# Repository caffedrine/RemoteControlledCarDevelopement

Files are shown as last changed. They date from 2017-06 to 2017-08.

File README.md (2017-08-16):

## RC Car Developement

Designing and implementing a remote controlled rover from zero to hero!

## Summary:
  1. Project information: [RC_Car_WordDoc.odt](docs/RC_Car_Developement.odt)
  2. Required list of components: [here](Components.md)
  3. How to build: [here](How-to-build.md)
  4. Firmware upload and debugging: [here](Firmware-upload.md)
  
*Costs:* ~60EUR

## Results

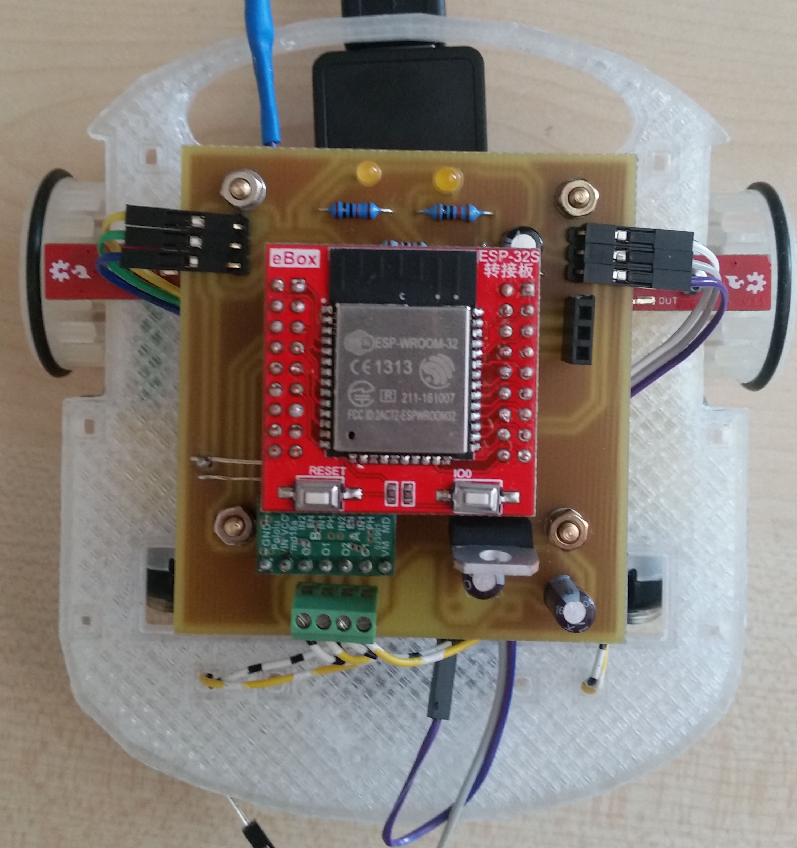
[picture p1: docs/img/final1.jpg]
final1

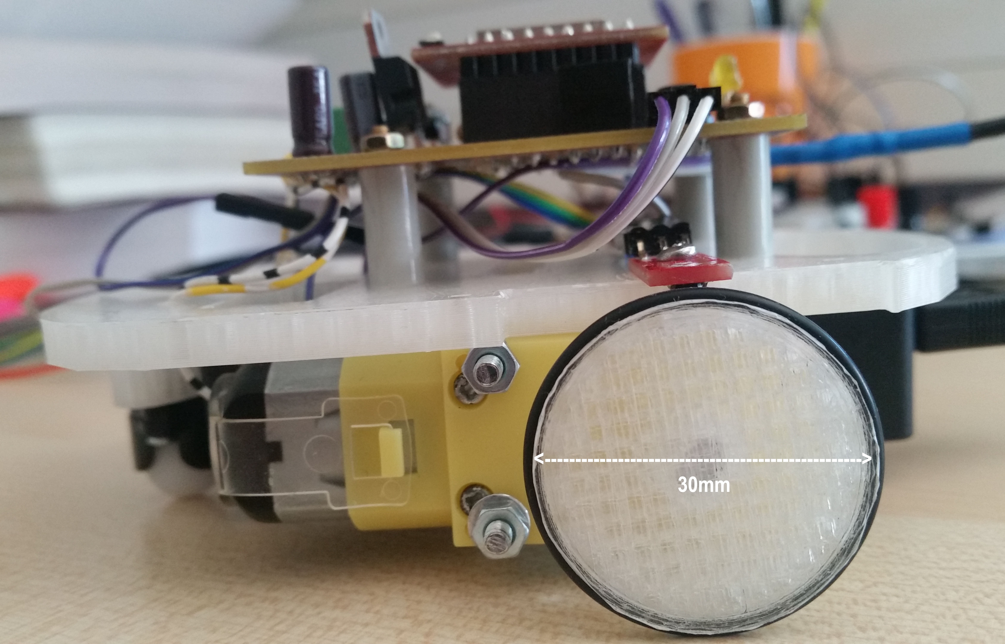
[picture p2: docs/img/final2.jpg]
final2


## Connections 

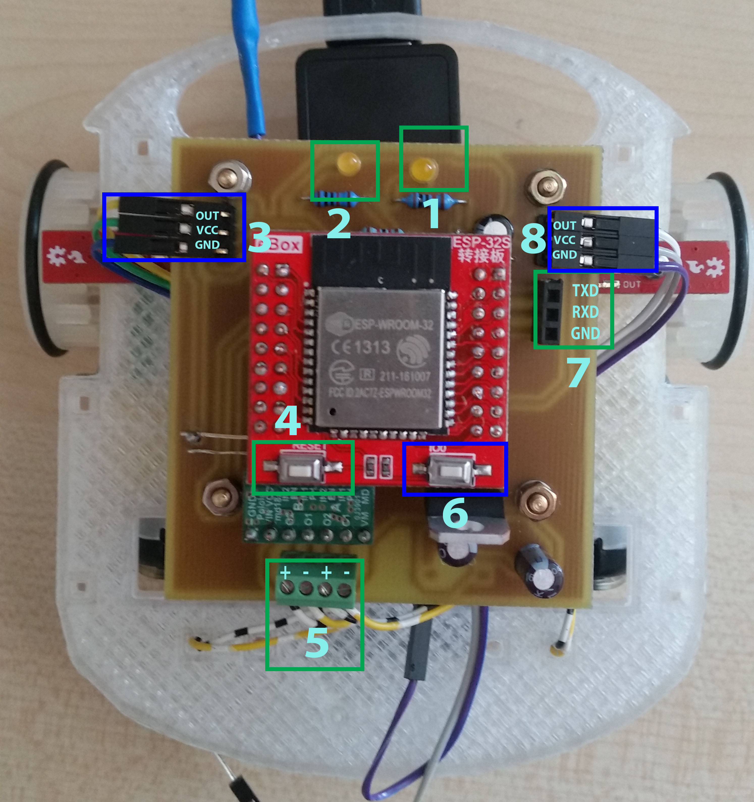
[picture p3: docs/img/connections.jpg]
connections


#### 1. Connection indicator LED
This is a LED whose meant is to indicate whether there is a connection established with car or not.
It have three states:
  1. Turned off - this mean that a connection is established with car and no further incoming connections will be accepted;
  2. Blinking - No clients connected to car AP nor Sockets are oppened;
  3. Blinking faster - Clients connected to AP but no sockets oppened. If use Java developed app, possibly application is not running.

#### 2. Traffic indicator LED
This is a LED whose meant is to act like any regular ethernet traffic indicator. Whether there is a data exchange between client and car this led will blink. Efficient feedback to confirm if your data is being received by car and vice-versa.

#### 3. Left QRE1113 IR Sensor
Connector for left wheel sensor.

#### 4. RESET Button
This is a push button which will reset car. Whether connection is not responding or you're unable to connect, presh this button and program will reset.

#### 5. Motors connector
Connect motors to this socket using the given pairs. First two entries for left motor and last two entries for right motor. In case motors are reversed, just switch polarity to get the correct rotation direction. 
PS: Do not cross connections between motors!!!

#### 6. IO0
This is a push button and is used to turn microcontroller into programming mode. Whether you want to upload a new firmware, you'll have to use this button in the following way:
Push IO0 and keep it pushed >> once RESET button (don't keep it pushed) >> release IO button. Now the microcontrolled will enter on programing mode and a new firmware can be uploaded using ping pins from point 7.

#### 7. Programming connectors
This is the socket used to upload a new firmware on mictrocontroller. Pins are active only when microcontroller is turned on on programming mode using point 6 (above).
Usually you coonnect pins to a Serial-2-USB converter.
**WARNING:** Logical levels are 0-3.3V. Applying 5V may broke the board.

#### 8. Right QRE1113 IR Sensor
Connector for right wheel sensor.

**Notes:**
  * future versions have a power switch on right-bottom edge;
  * micro USB connection is in bottom layer right beside motors connector;

## How to control the car
Turn the power on by connecting cable to powerbank and swith on. After few seconds, connection led should blink indicating that car is waiting for a incomming conenction. To control the car, two connection phases are required:
1. Connecting to AP - This is the exactly like connecting to any regular router or hotspot. This is possible because car will automatically will create an Access Point (hotspot) when is powered on. Just connect to that network!
In order to do this, you will need **AP Name** and **password**. Check here for credentials: [firmware](Arduino/)
Windows instructions: https://support.microsoft.com/en-us/help/17137/windows-setting-up-wireless-network

2. After you are connected, the connection led will blink a little bit faster. Now, now we need to make sure we are connected to right network. 
The following tool is required: [putty](http://www.putty.org/) - download and install PuTTy.
Launch and fill IP address with **192.168.4.1** and port **1337** and select "Telnet" for protocol, as in the following picture:

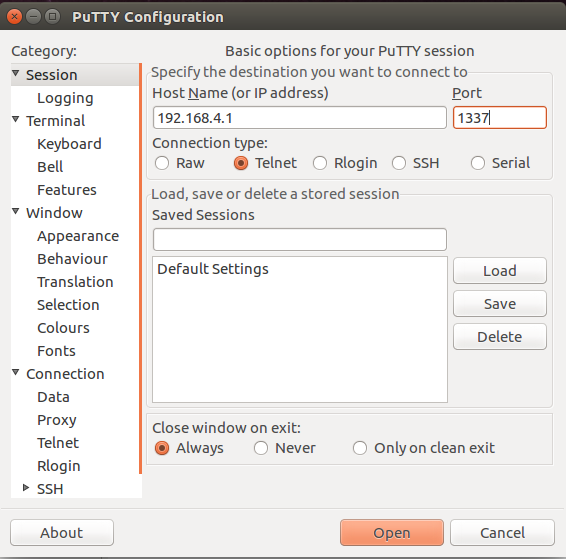
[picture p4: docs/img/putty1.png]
Putty connecting


Then click open button (bottom).

At this point communication channel should be established with car. If everything is fine, the connection led should not blink anymore and you will get the following window:

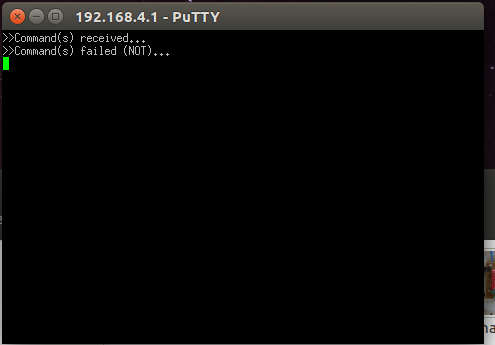
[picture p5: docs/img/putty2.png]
Connection established


We can use this terminal to send commands to car:
For example, type **>>>[G;20;3000]** and hit *Enter*. At this point, car will give feed back when command is received and executed:

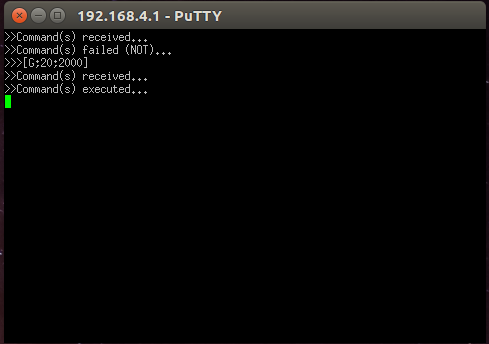
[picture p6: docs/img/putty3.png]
Sending commands


Details about commands here: [Java Commands](Java/)

At this point, you can made your own application with joysticks and stuff and use TCP sockets to send commands! Check my other repositories as I already made some C++ and Qt Wrappers for TCP Sockets. Check Java folder as WiFi.java may be public :)

**Note:** You can also use mobile phone but use an application such as *Mobile Telnet* instead of PuTTy.

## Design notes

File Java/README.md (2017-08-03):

# JAVA Source code

Not updated as requirements for this code was not to be published!
However, there is an password protected archive with Java source code: **controldeveloper.zip**

## Major to original project

PS: Old code is just commented.

#### A. Under **src/hsrt/mec/controldeveloper/core/com**:
  1. Added new class: **WiFiCard.java**
  2. Added new class: **WiFiCardHandler.java**
  3. Changed **BackgroundControl.java**
      * Added function *private void waitForResponse(int timeout)*
      * Changed line 59;
      * Adeed lines 65-82;
  4. Changed **ComHandler.java**
      * Changed function **private MotorCommand computeDirectionCommand(IDirection command)**;
      *	Changed function **private MotorCommand computeGearCommand(IGear command)**
  5. Changed **MotorCommand.java**
      * Rewritten **String getCommandString()**

#### B. Under **src/hsrt/mec/controldeveloper/core/com/test**:
  1. Added new class: **WiFiCardHandlerTest.java** -> this class is used to test Wi-Fi connection with the car. The model is the same like the other as the other tests.

#### c. Under **src/hsrt/mec/controldeveloper/io**
  1. Added new class **WiFi.java**
  
#### D. Under **src/hsrt/mec/controldeveloper/util**
  1. Changed **Globals.java**
      * Appended some more global variables.
      
## Explained changes:     
The car only accept the following instructions in the following format:
  1. Direction: **>>[D;\<degrees\>;<0>]** 
     * where degrees is in interval: [-90, 90] and is the angle you want to make;
	 * examples: >>[D;90;0] - rotate to right 90 degrees; [D;-90;0] - rotate to left 90 degrees.
  2. Gear: **>>[G;\<speed\>;\<duration\>]**
     * where speed is a value in interval [-100, 100]; where -100 is 100% power backward and 100 is 100% power forward;
     * examples: >>[G;80;5] - move forward for 5 seconds with 80% power; >>[G;-50;2.5] - move backward with 50% power for 2.5 seconds;
  3. Pause: **>>[P;\<duration\>;<0>]**
     * where duration is the duration for car to hold brakes;
     * examples: >>[P;5;0] - car will stop any action for 5 seconds;

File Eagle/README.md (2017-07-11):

# Eagle files for PCB!

# Pinmap: 
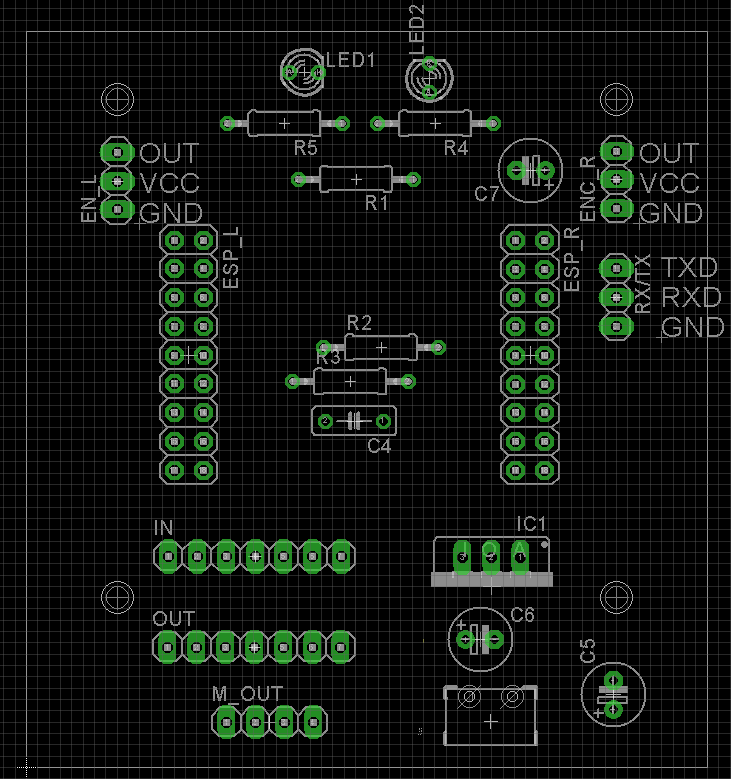
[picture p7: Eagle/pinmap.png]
rc car pinmap PCB Pinmap


# Schematic
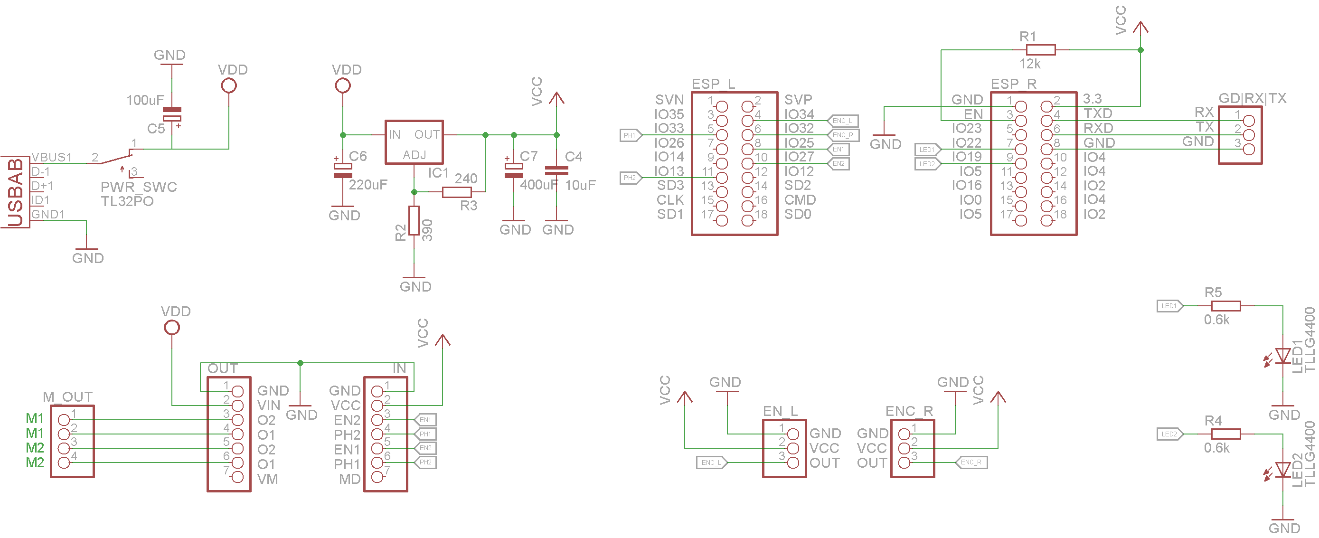
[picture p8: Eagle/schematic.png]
schematic


# Final PCB
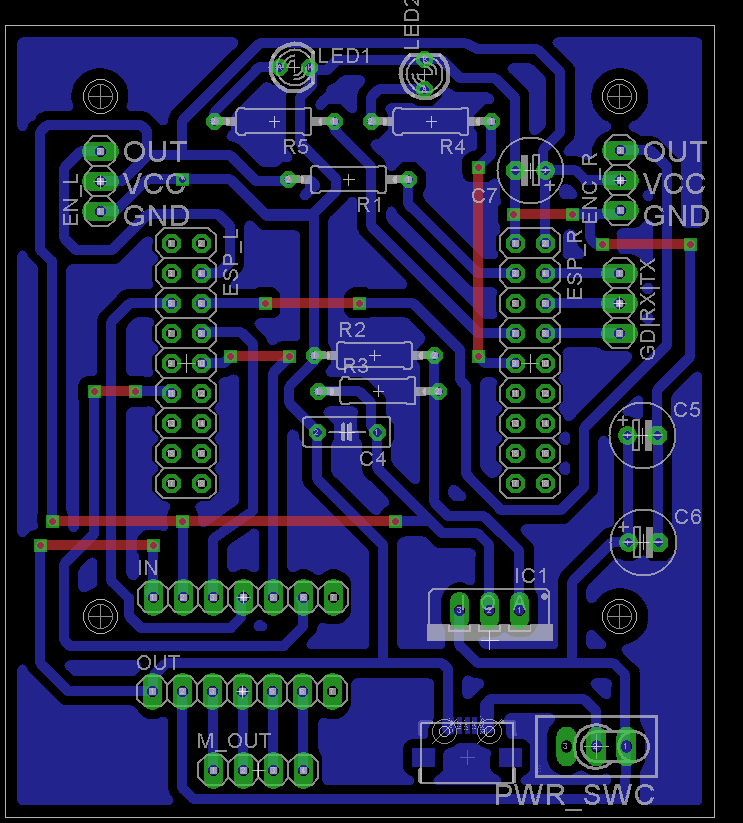
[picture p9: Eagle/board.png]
final_pcb


# Physical PCB
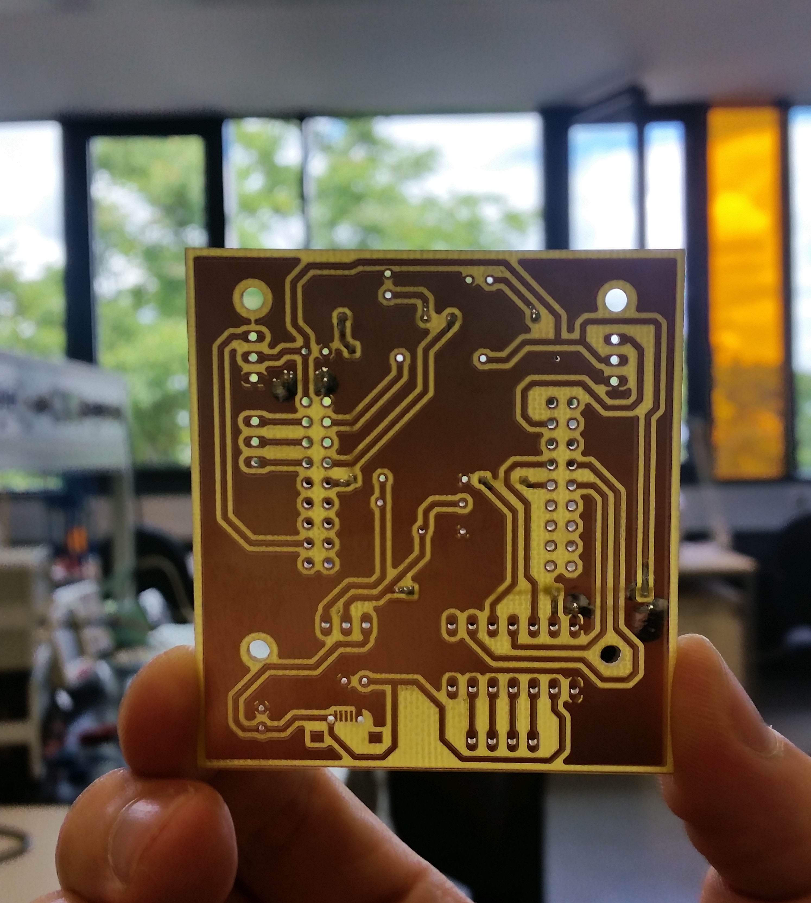
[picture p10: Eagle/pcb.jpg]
phisical


# Physical Board
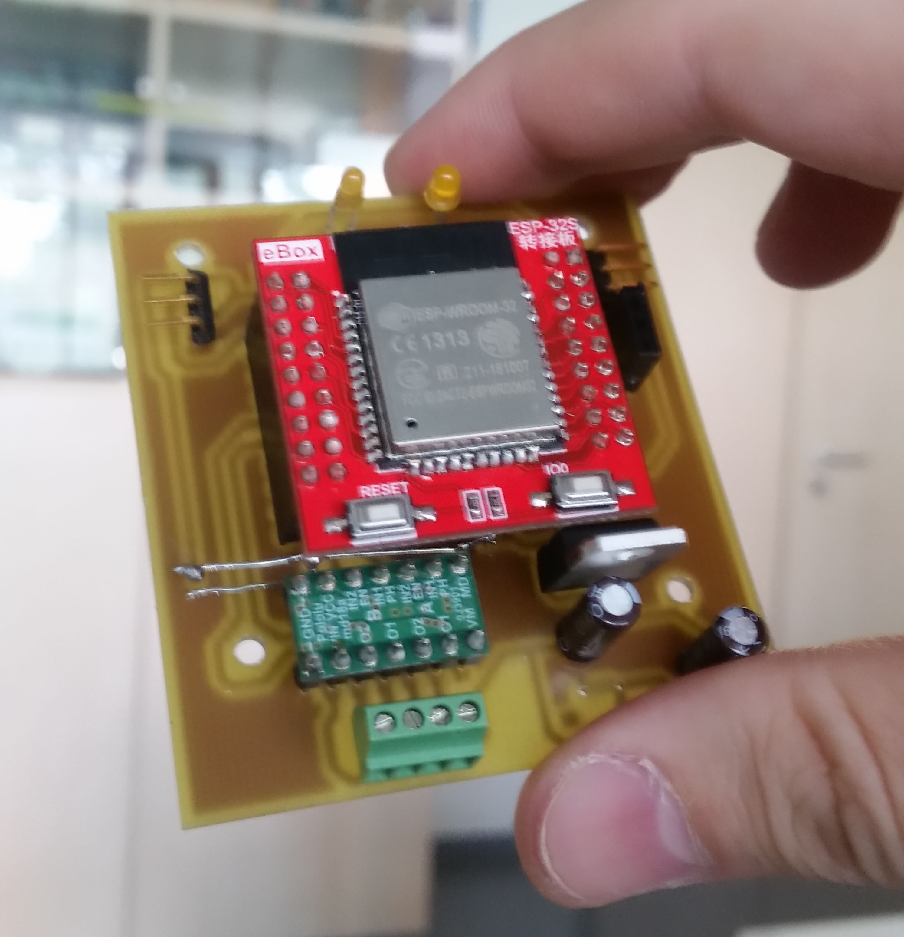
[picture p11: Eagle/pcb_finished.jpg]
pcb


## Tip:
  1. You can add an heat sink in case LM317 Voltage Regulator is getting hot.

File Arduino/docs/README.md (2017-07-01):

# Usefull maps

# ESP32 Thing - Pinmap
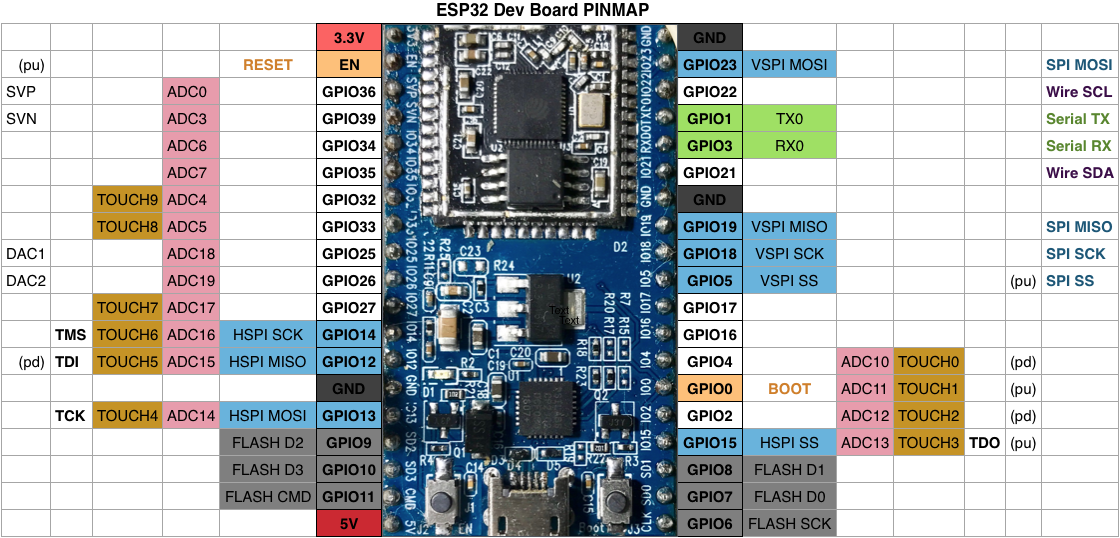
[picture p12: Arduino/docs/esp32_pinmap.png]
ESP32 Thing - Pinmap


# ESP32 Thing - Pinmap 2
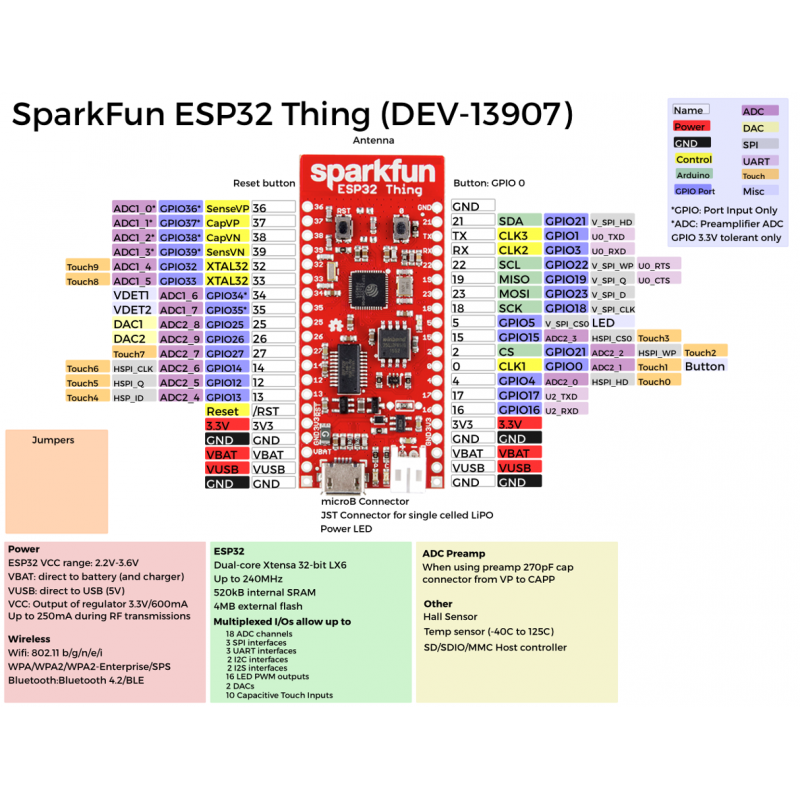
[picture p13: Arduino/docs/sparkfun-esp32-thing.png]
ESP32 Thing - Pinmap 2


# ESP32 WROOM - Pinmap
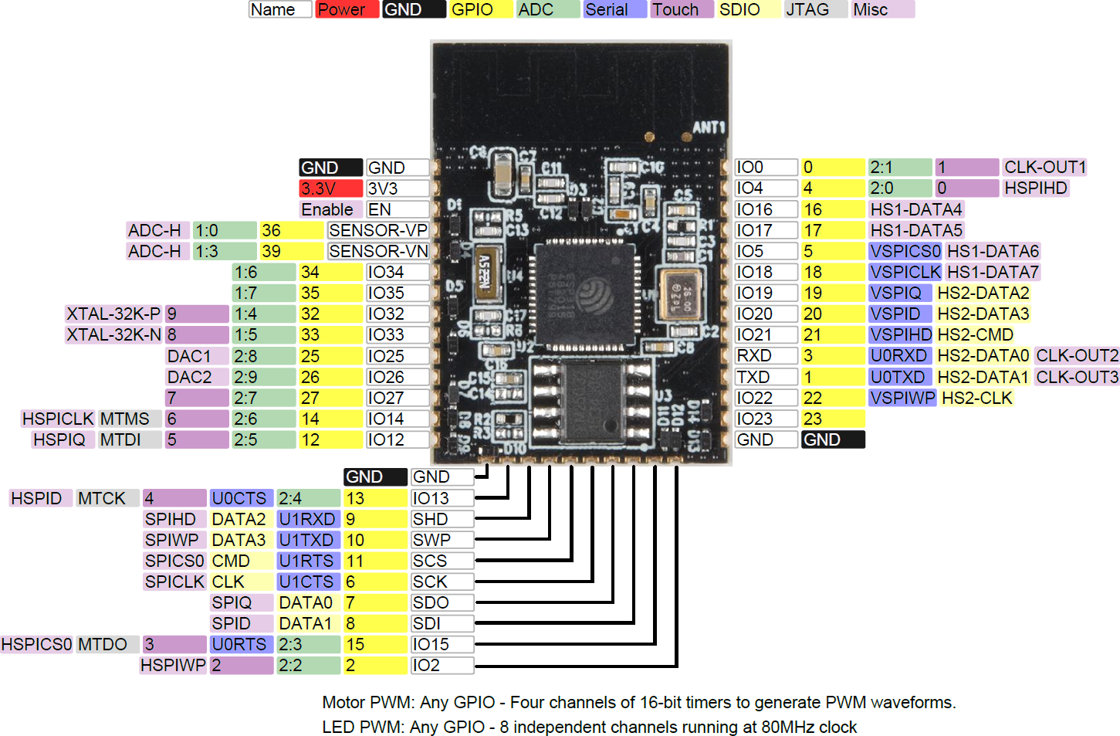
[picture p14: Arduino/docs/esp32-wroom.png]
ESP32 WROOM - Pinmap


# ESP32 WROOM - Pinmap2
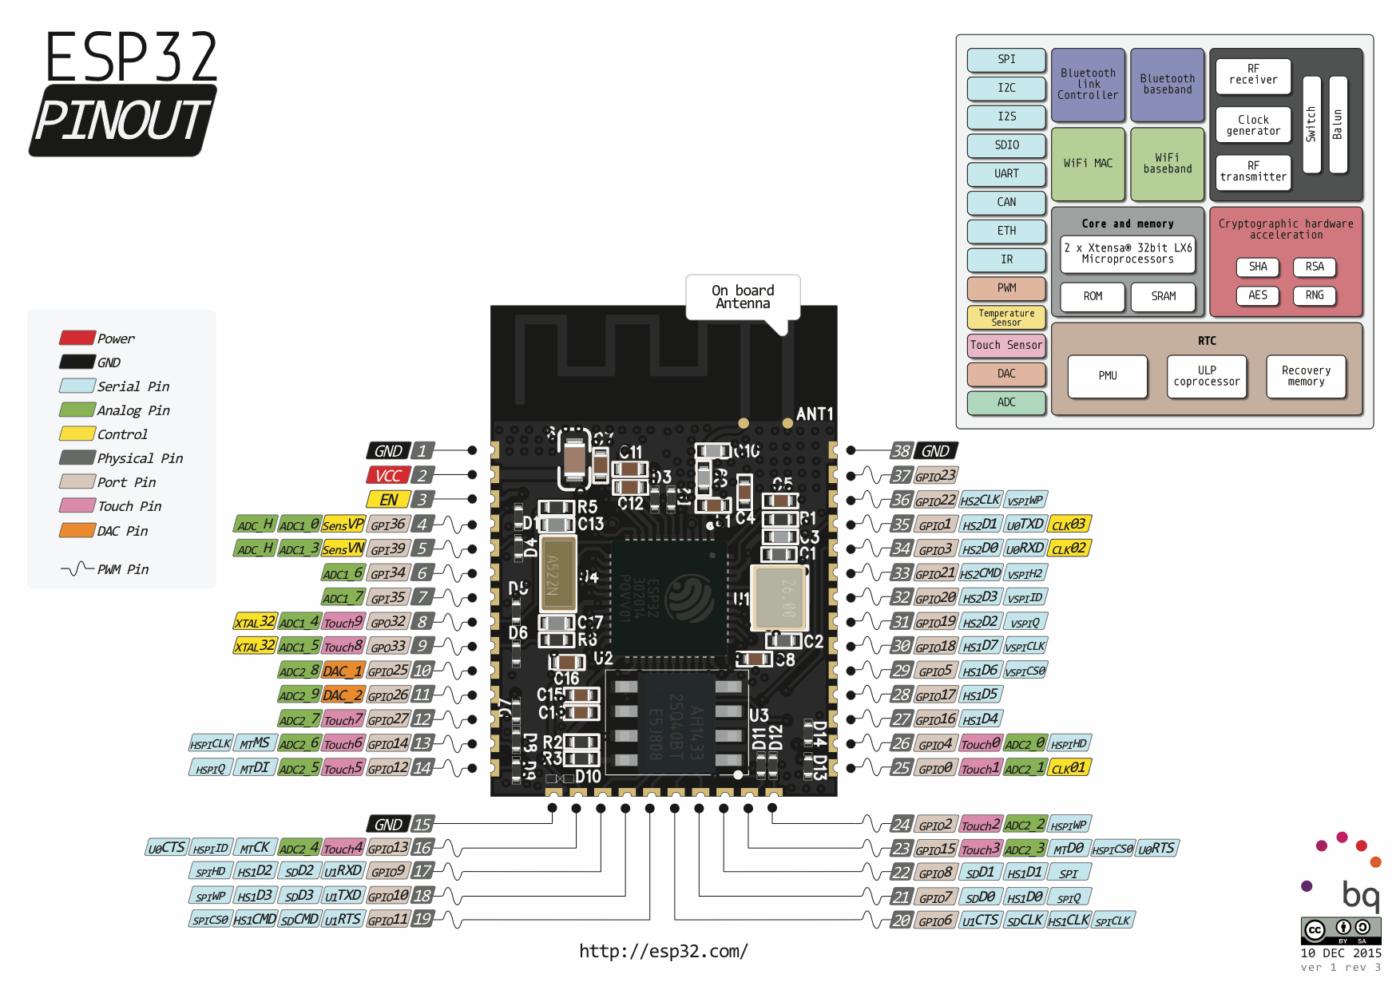
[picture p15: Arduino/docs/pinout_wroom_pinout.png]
ESP32 WROOM - Pinmap


# ESP32 WROOM Adapter - Pinmap
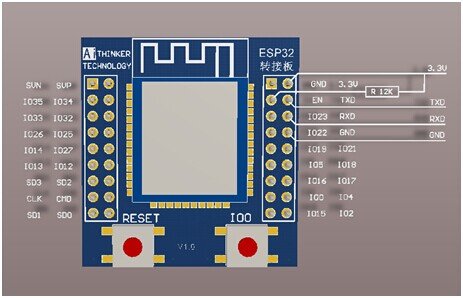
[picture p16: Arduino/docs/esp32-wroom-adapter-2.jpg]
ESP32 WROOM Adapter - Pin map


# ESP32 WROOM Adapter - Pinmap2
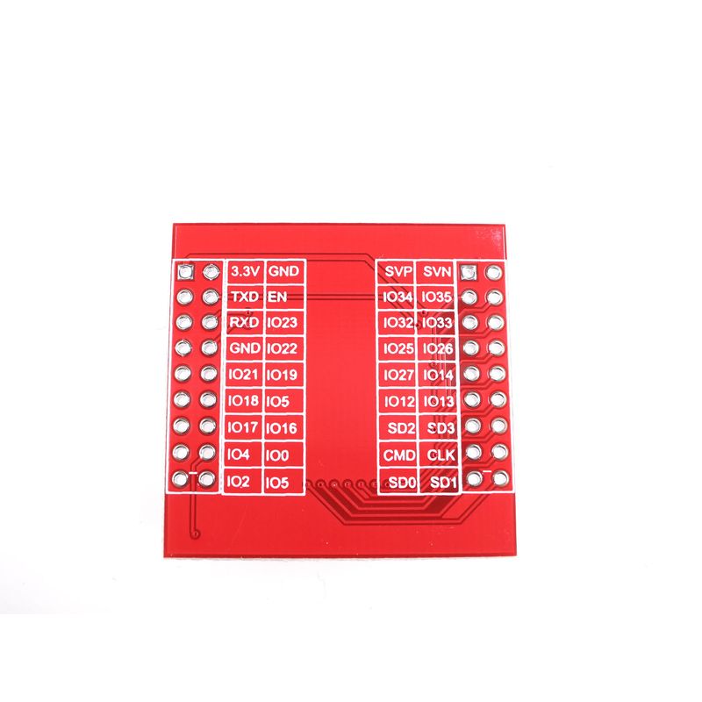
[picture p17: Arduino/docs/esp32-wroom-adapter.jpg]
ESP32 WROOM Adapter 2 - Pin map


# ESP32 WROOM - Programmer
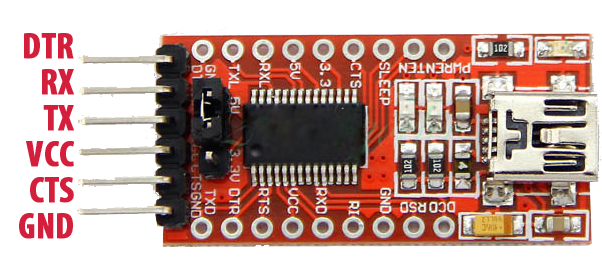
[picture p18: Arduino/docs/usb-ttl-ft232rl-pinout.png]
ESP32 WROOM Adapter 2 - Pinmap


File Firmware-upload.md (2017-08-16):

# Firmware

## 1. Connection

Debugging and firmware uploading share the same connection. No matter if you want to debug or to upload a new version of firmware, connection instructions are the same, always!

The connection to car is via Serial port with a baud rate of **115200**. The other settings are default and should not be changed.

Usually the computer already comes with serial ports **BUT** it's logic level is 0-5V which makes it incompatible with the designed car as it equire 0-3.3V as operable logical levels.

In order to do this, it's recommended to use a serial adapter such as the following one: 

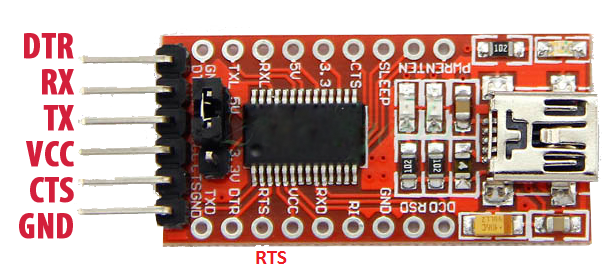
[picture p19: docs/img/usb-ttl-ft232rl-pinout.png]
serial adapter


WARNING: Don't forget to set juper on 3.3V, as in picture:
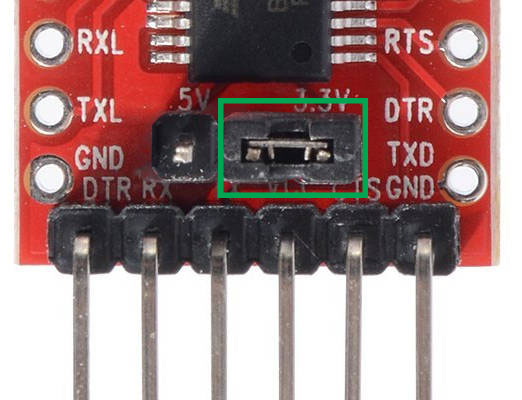
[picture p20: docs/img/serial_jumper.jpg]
jumper


Don't forget also about mini USB cable used to connect adapter to computer:
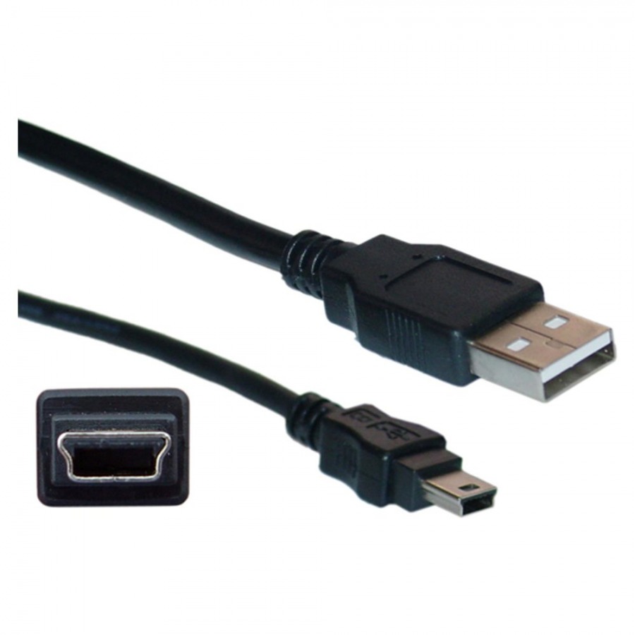
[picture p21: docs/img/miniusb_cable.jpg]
miniusb cable


And the witing should looks like this:
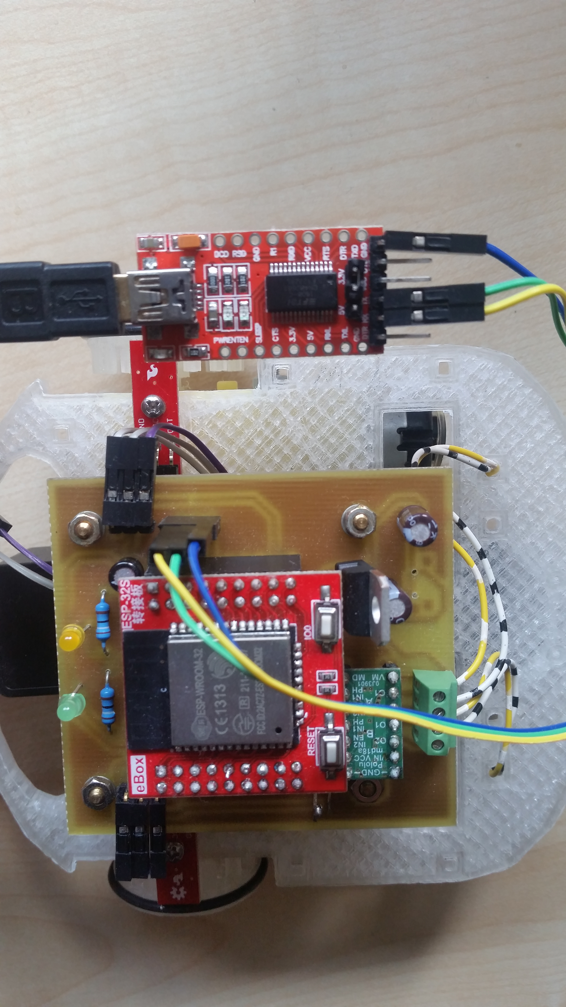
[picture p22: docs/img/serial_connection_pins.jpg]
serial connection


The pins which shuld be connected in this order to debugging port:

~~~
Adapter -> Car
RX -> PIN 1
TX -> PIN 2
GND -> PIN 3
~~~
Not that we have everything connected, we have two powwibilities: debug or upload firmware

## 2. Debugging 

To receive debugging data, we'll use PuTTy application: http://www.putty.org/
Download and install application.

Open application, select Serial port, set boud rate to 115200 then click open.
PS: Under linux, launch putty from terminal with sudo permission ($ sudo putty) and use port name **/dev/ttyUSB0**.
PS1: If you have other serial devices connected, you may have to change it to the correct one. On windows COM1 -> COM2 and on Linux /dev/ttyUSB0 -> /dev/ttyUSB1
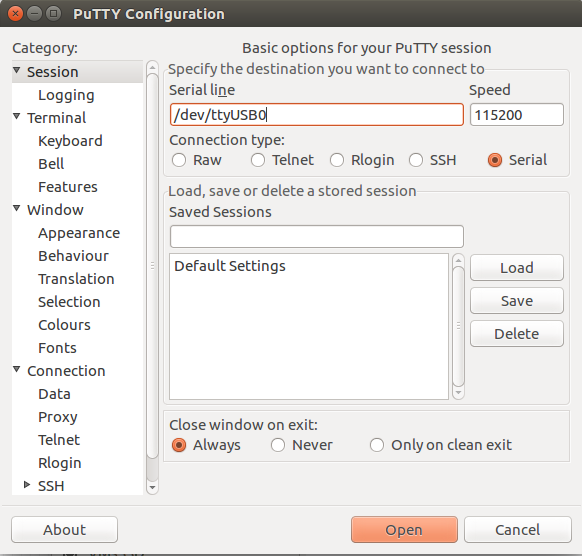
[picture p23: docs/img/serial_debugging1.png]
serial connection


After putty launches a new terminal, press reset button from top of the car and the terminal will display current state of car:
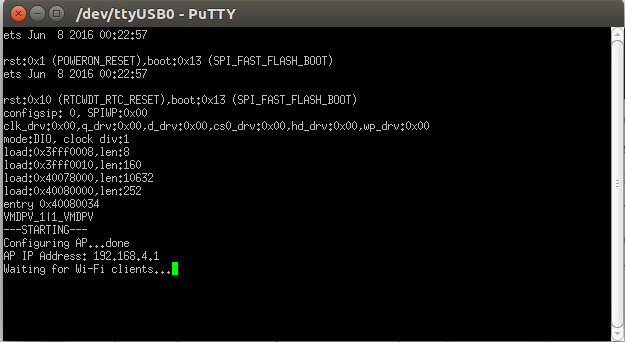
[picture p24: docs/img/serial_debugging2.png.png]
serial connection2


Now connect to car from regullar application and terminal will display data every 0.5 seconds in the following format:
 \<SIDE\>: steps/\<time\> (\<analogic_output\>) Count: <counted_steps>

Example: R: 3/t (3400) Count: 133 -> right right wheel speed is 3/t and have counted till reset a number of 133 steps.

Now you can rotate the wheels and check the accuracy of sensors or if sensors are working as expected!

If you need to recalibrate sensors, the c++ file **QRE1113_Driver.h** from *Arduino/ControlDeveloper_ESP32Wroom* folder according to it's documentation.

## 3. Uploading new firmware

It's the same procedure as uploading code to ESP32-Wroom board.

1. You'll need to install the following softwares:
     a. Arduino IDE: https://www.arduino.cc/en/Main/Software
     
     b. ESP32 Support: https://github.com/espressif/arduino-esp32/blob/master/doc/windows.md
 
2. Now open .ino file from *Arduino/ControlDeveloper_ESP32Wroom* with Arduino IDE.
3. Configure IDE:

     a. Select the correct serial port: Tools -> Port
     
     b. From Tools >> Board select **FireBeetle-ESP32**
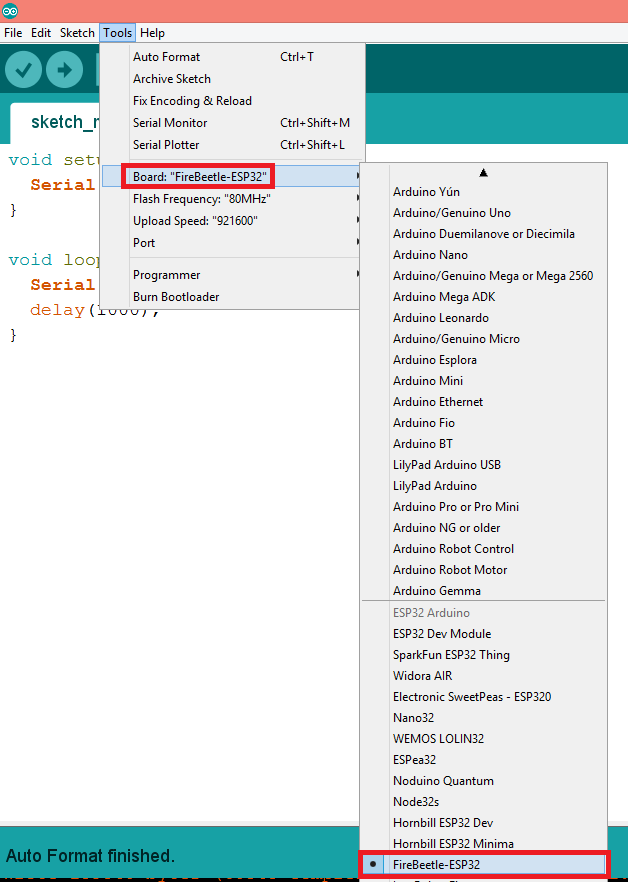
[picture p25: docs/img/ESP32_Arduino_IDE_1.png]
board
     
     
     c. Tools >> Flash Freq -> 80MHz, Upload speed -> 921600
4. Turn car into programming mode: Push reset button + IO button from the top of car and release first reset button and then I0 button. 
5. Click un upload button.

At this point, the bottom console will display messages regarding progress and whether operation succeed or fail.

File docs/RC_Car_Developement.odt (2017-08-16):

RC Car Development

1. IDEA

We would like to develop a remote control car, which should be controlled via an Java application using a regular computer/laptop with a Wi-Fi chip.

2. REQUIREMENTS ENGINEERING

1. The RC car shall be controlled by a process defined in the Control-Developer GUI

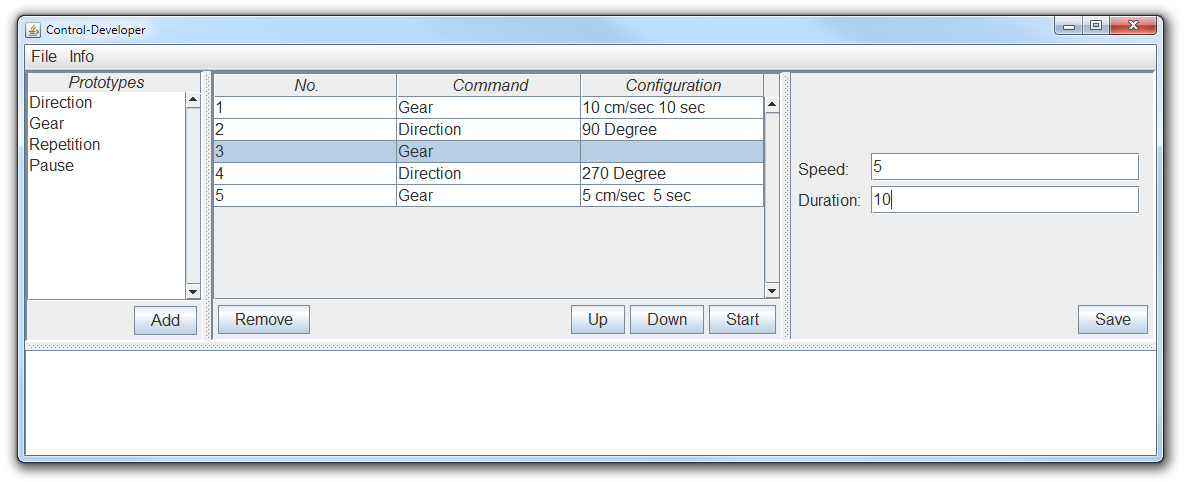
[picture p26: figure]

2. The connection between the Java GUI and the RC car shall be based on WiFi.
3. The Control-Developer GUI has to be expanded by setting up the connection out of a set of connections
4. The functionality for transmitting the data to the RC car shall be integrated into the overall Control-Developer GUI framework by extending the existing framework.
5. After pressing the “Start” button the RC-car shall start moving regarding the selected command; commands are
  a. Gear drive for x sec. with the speed of y
  b. Direction turn x degrees (x < 0: turn left; x>= 0: turn right)
  c. Pause do not move for x sec.
6. The commands shall executed sequentially.
7. The RC car receives one command, executes it and sends a response after finishing execution.
8. The movement of the car shall be such precise, that you can take a “ruler” and the car shall follow the polygon.
9. There should be an error handling regarding the connection to the RC car (time out regarding feedback of the RC car). Possible answers from the RC car would be
  a. Command Successfully Received
  b. Command Successfully Executed

3. ANALYSIS

a. Logical structure

The logic of the whole system works as shown in the following diagram:

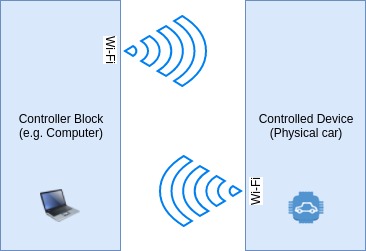
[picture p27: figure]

The system consists of two main logical blocks:

1. Controller Block;
2. Controlled Device [Block];

The communication established between those two blocks is full-duplex, this mean that both blocks will be able to send and receive data at the same time. Master-Slave principe is used.

The protocol which will used in order to establish a communication channel between main two blocks is Wi-Fi. In this case we have two options rgarding Wi-Fi frequency: 2.4GHz and 5GHz:

Protocol | Range | Bandwidth | Interferences | Compatib. | Costs
2.4GHz | High | Low | High | High | Normal
5GHz | Low | High | Low | Normal | >Normal

Data amount exchanged by our system is fairly low; further more, we want the range to be as high as possible so 2.4GHz Wi-Fi protocol will be used in the designed system.

The format of data exchanged and conventions will be defined in implementation chapter.

1. Controller block

This block is represented by a device which acts like a master in the system. It can be a computer or any other device wich is able to run the designated Java application and has a Wi-Fi chip.

From this block all commands are send to the car; also this is the block which listen to the response from car; whenever a command is send, two responses are expected: confirmation of command received and confirmation of command executed.

The very last layer of this his block also contain the GUI used by a user to send commands to the car.

2. Controlled Device [Block];

This block is also divided in other hardware modules placed on the car, like in the following diagram:

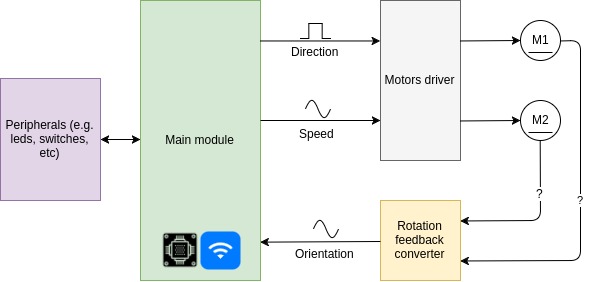
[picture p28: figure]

Main module is the „brain“ of the car. This module process the command received from the Java application then it translate is for motors. The calculations regarding direction correcting are processed here.

The following logical blocks are implemented at this level:

1. Main module (C&C);
2. Motors driver;
3. Rotation feedback converter (data used in order to detect angular velocity);
4. Peripherals

1. Main module

This module has the microcontroller used to process data and it also contain the Wi-Fi communication module and a Bluetooth module. One of the strengths of using this kind of module is that we don't worry about Wi-Fi and TCP/IP suit implementation.

Commands from the computer (controller) arrive here though Wi-Fi. In this block all commands and informations are processed and then routed to their destinations. Also some data integrity checks can be performed here.

2. Motors driver

This module have 4 inputs (connected to main block) and two high power outputs (connected to motors) organised as the following:

Inputs:

1. Motor1:
- Speed (Analogic signal);
- Direction (Digital – Usually, 1 = forward and 0 = backward);
2. Motor2:
- Speed (Analogic signal);
- Direction (Digital – Usually, 1 = forward and 0 = backward);

Outputs:

High power output ports in order to supply and command motors.

3. Rotation feedback converter

Rotation feedback block provide provide data related to current orientation or motors position. This data is used as a feedback for main module in order to execute commands with high level of accuracy.

Pins mode:

1. 2 Inputs (connected to motors) – Signals: motors current value;
2. 2 Outputs (connected to main block) – Current value converted to analogic unit supported by main block;

4. Peripherals

Basically all auxiliar components or devices such as led, battery level indicator, etc;

b. Hardware components

1. Main module

The main module consists of an Espressif ESP32 ESP-WROOM-32 WiFi/WLAN+Bluetooth Module.

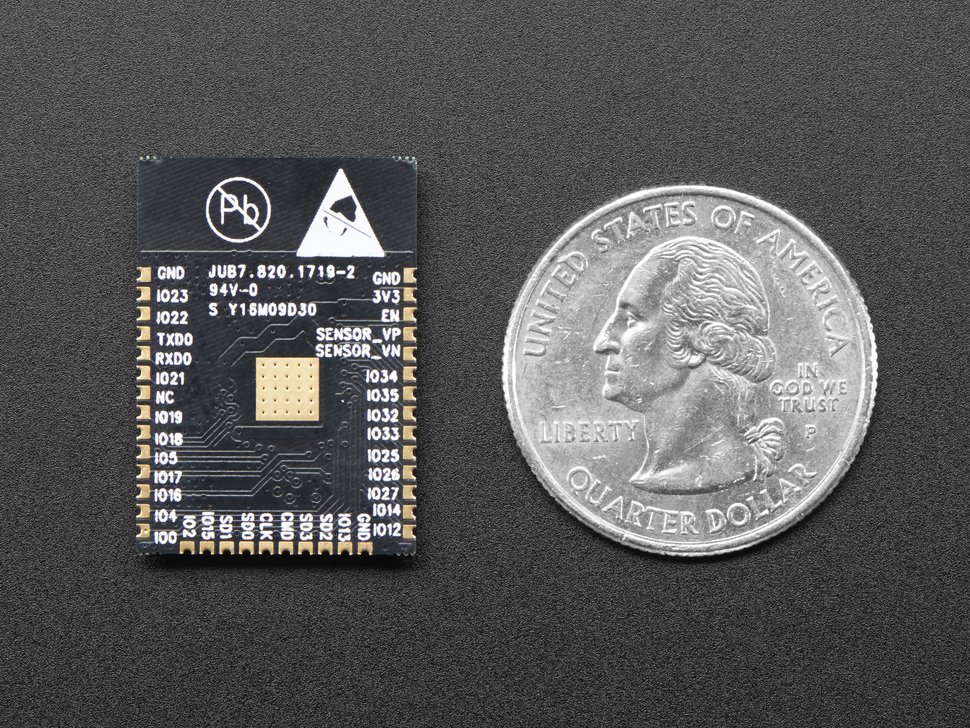
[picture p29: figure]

As previously said, this module include the communication Wi-Fi and Bluetooth communication chips and also a uC which can be used to process our data and commands. This module alse come with

Also a bunch of GPIOs pins are provided in order to interact with our controlled device.

2. Motors driver

To control motors is relative simple, because DC motors are used. Basically, varying tension, the speed and direction will also vary. Because we need a high amount of power on the motors, we can't connect them directly to uC. To achieve this, a H bridge for every motos is required. However, a better option would be to just buy a driver as it will be smaller and reliable.

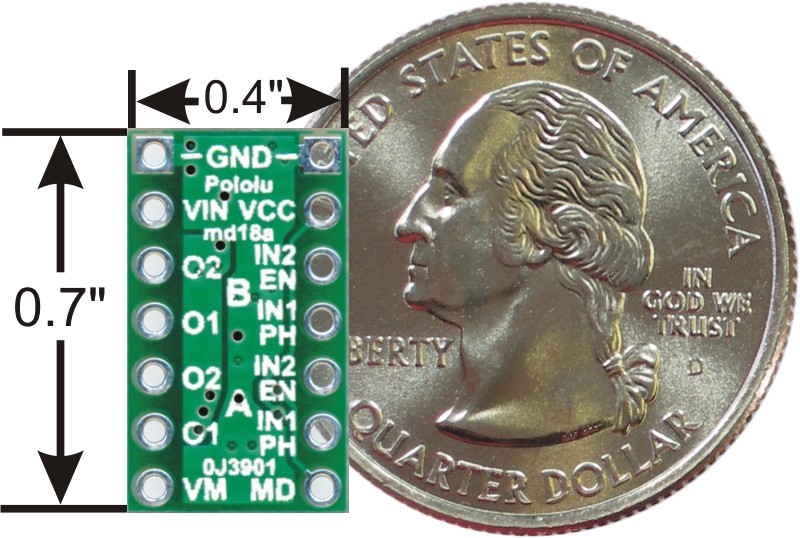
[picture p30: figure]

The chip used is Pololu DRV8835 Dual Motor Driver Carrier. Is support booth two motors.

The chip is also commanded by main microcontroller, which is integrated by communication module.

3. Rotation feedback converter

The name of this block looks like a generic name and it is as we have few options in order to achieve goal of accuracy rotations.

Method | Costs | Complexity | Space required | Efficenty
Motors encoder | Normal | Normal | High | Low
9-DOF IMU | High | Normal | Normal | High
Ampermeter | Low | Low | Normal | Low
Gyro+Acc | Normal | High | Normal | Normal

The highlighted method will be used.

For ampermeter method, basically, the current consumed by every motor is measured then converted into analogic unit in order to be send to uC. On microcontroller, both values of the motors are compared. Form those values the direction can be calculated. Now that we know actual direction of car, all we have to do is to compare that with the direction required by user; if it is not the same, the uC will try to correct it.

c. Context diagram


d. Dataflow diagram

1. Main processes


2. Logical model of processes


4. Design and implementation

Designing and implementation is presented using Markdown format files and can be found in .md files spread across project folders.

I recommend reading of .md files directly on GitHub or using a tool such as markdown offline viewer: http://www.texts.io/download/

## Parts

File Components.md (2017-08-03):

# List of components
Before proceeding, make sure you have the possibility to print the frame of car using a 3D Printer! It is in folder 3D_Design. Also don't forget to print the wheels!
Also make sure you have the possibility to create Printed Circuit Boards (PCB).

### Main components required:
  1. **2x QRE1113** - SparkFun RedBot Sensor - Line Follower
     https://eckstein-shop.de/SparkFun-RedBot-Sensor-Line-Follower
  2. **2x DC Motors + GearBox** - Recommended gear ratio: 120:1
     http://www.exp-tech.de/dagu-dc-gear-motor-paar-90-degree-shaft-120-1
  3. **1x DRV8835 Dual Motor Driver** - In case you don't want to make your own H bridges.
     http://www.exp-tech.de/drv8835-dual-motor-driver-carrier 
  4. **1x Espressif ESP-WROOM-32** - This is the WiFi 2.4 GHz module used to control car.
     https://eckstein-shop.de/Espressif-ESP-WROOM-32
  5. **1x Wifi Module Adapter** - This will make life easier
     https://eckstein-shop.de/Adapter-Breakout-Board-fuer-ESP-32S-ESP32-ESP-WROOM-32-Wireless-Bluetooth-Module
  6. **1x Plastic Wheel Ball**
     http://www.exp-tech.de/pololu-ball-caster-with-1-2-plastic-ball?gclid=CKmr-tb2h9QCFUklgQode0oNgg
  7. **1x Powerbank** - You can also find this on Amazon at better prices.
     https://www.tln-werbemittel.de/powerbanks/powerbank-akku-tower-38-2600.html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
  8. **2xRubber O-Rings** - In order to get some aderency on wheels.
     https://www.hug-technik.com/shop/product_info.php?info=p20325_praezisions-o-ring-30-00-x-2-60-mm-nbr70.html
  9. **1xUSB Micro B Connector**
     http://uk.farnell.com/amphenol-fci/10104110-0001lf/micro-usb-2-0-type-b-receptacle/dp/2293753
  10. **Power ON/OFF switch**
      https://eckstein-shop.de/Adafruit-Breadboard-friendly-SPDT-Slide-Switch-Schiebeschalter
  11. **6.5mm Screws**
  	  https://www.conrad.biz/de/blechschrauben-22-mm-65-mm-kreuzschlitz-philips-din-7981-c-edelstahl-a2-100-st-liko-a2-839536-839536.html
     
### Electrical components:
  1. 1x LM317 Voltage regulator
  2. 2x Reasonable leds
  3. 10x Pinheaders Male
  4. 25x Pinheader Female
  5. 2x 20 Double Pinheader Female
  6. 2x Reasonable leds
  7. 2x 0.6~0.9K Resistors
  8. 1x 12k Resistors
  9. *1x 390 Ohm Resistor*
  10. *1x240 Ohm Resistor*
  11. Electrolithic capacitors: 1x100uF, 2x220uF or lower.
  12. Ceramic capacitors: 1x10uF  

### Components/Tools required to build prototype
  1. **1x FTDI1232** - This is an adapter which allows you to write program to WiFi Module. You can make your own it's not hard but be aware that you need to convert logical levels from USB from [0-5V] to [0-3.3V]
     https://www.amazon.de/AZDelivery-Adapter-FT232RL-Serial-Arduino/dp/B01N9RZK6I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
  2. **Optional:** If you want to test and debug code easily, you may want to pick up an Sparkfun ESP32 Thing - Developement board. Build code on that board and upload to ESP32-WROOM when it is finished.
     http://www.exp-tech.de/en/sparkfun-esp32-thing?___from_store=de

#### Other components
Screws, wires, zipties and stuff like this :)
	 
**PS: If the links expired, let those guys know: http://web.archive.org **

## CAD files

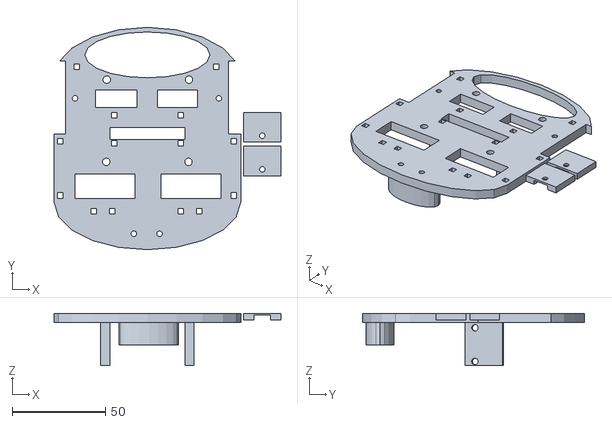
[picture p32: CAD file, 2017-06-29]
3D_Design/RoverFrame.stl
121.5 x 119.0 x 28.0

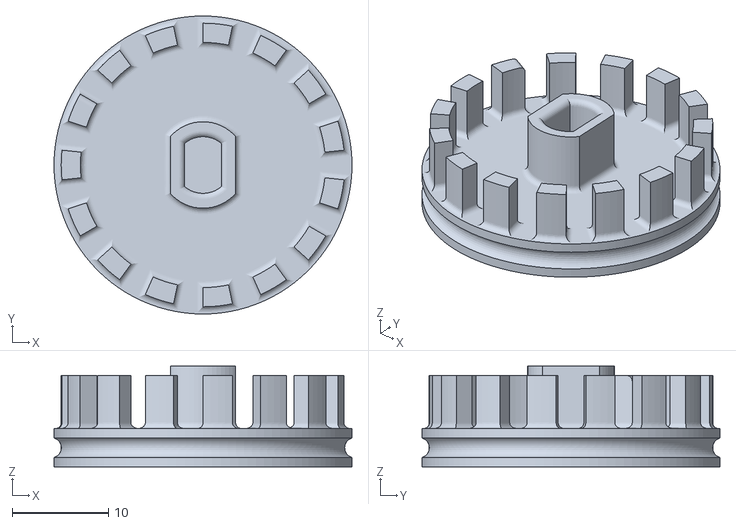
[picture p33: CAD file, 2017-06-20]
3D_Design/Wheel - (c) Anian B.stl
31.0 x 31.0 x 10.5

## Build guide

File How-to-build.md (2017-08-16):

# How to build:

### 1. Frame printing:
First of all you will have to print frame from **3D_Design** folder:
1x RoverFrame
2x Wheel

PS: There are multiple formats for RoverFrame. Choose the one compatible with 3D printer.

At the end you'll have something like this:
Frame printed

### 2. Print electrical design (PCB)
In folder **Eagle** you will find electrical schematic and pcb design and some helpfull notes. Software used to design circuit schematic and PCB was **Eagle v6.1** and project files are under *Eagle/controldeveloper/*.
Create the PCB using a CNC machine or using *home made* method.

After you printed PCB, solder all components according to schematic and instructions from **Eagle** folder.

At the end, you'll have something like this:
PCB Finished

### 3. Assemble all components like in the following pictures:
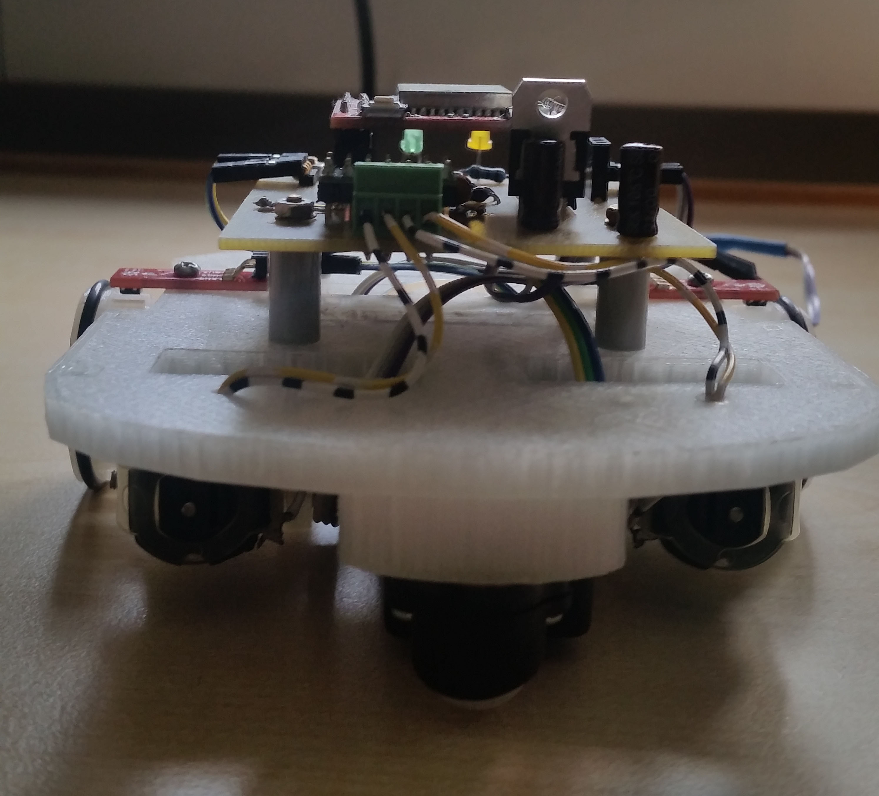
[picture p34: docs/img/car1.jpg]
car1

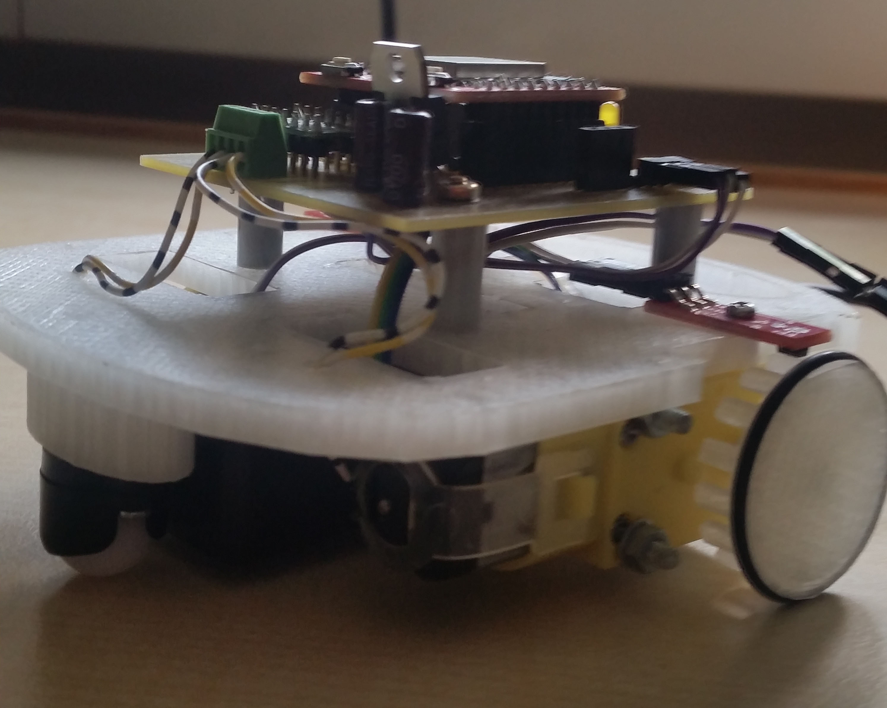
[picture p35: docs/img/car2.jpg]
car2

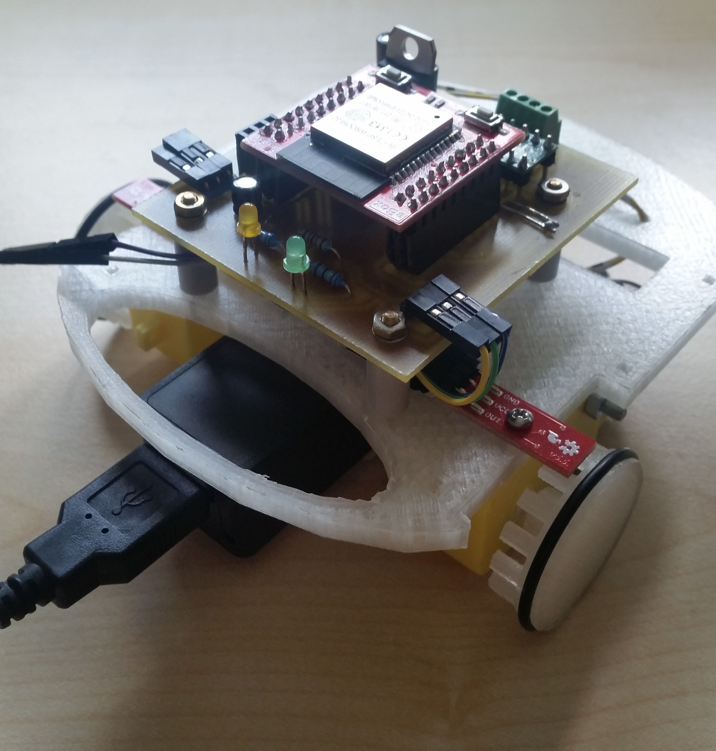
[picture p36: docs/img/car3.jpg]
car3


# Additional building tips
  1. If you will try to compile Firmware and upload it from a Windows machine, it will take almost half minute (I7 + SSD) for code to be uploaded on ESP board and even more if you have installed an antivirus with ransomware protection enabled. My advice, use Ubuntu when debugging or improving the Firmware. It will be way easy and faster.
  2. Be carefull at battery. A powerbang which provide only 800mA on output may not be be enough. Sometimes, when WiFi Radios are enabled on ESP Board, motors and ESP Board need more current feed. When those peaks are reached, ADC ports may get crazy!
  3. If something is not working, connect serial cable and check debug logs received via Serial port. It is enabled by default. 
  4. If you customize the firmware and Eagle Schematic/PCB, make sure you don't use ANALOG PINS FROM CHANNEL 2 neither DACS. Won't work when radios are enabled. Yes! When WiFi radios are enabled, only ADC pins from channel 1 are usable as ADC Input ports. Of course, you can use those pins as digital or even PWM.

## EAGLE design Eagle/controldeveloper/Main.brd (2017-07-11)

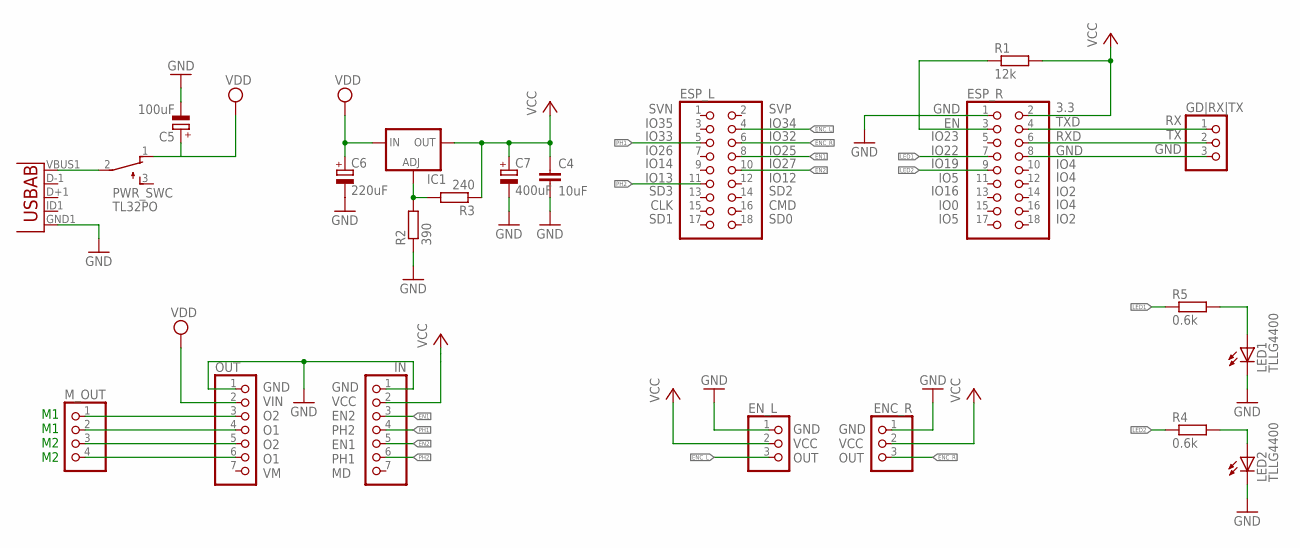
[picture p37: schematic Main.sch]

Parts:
C4: 10uF; C050-025X075
C5: 100uF; E2,5-6
C6: 220uF; E2,5-6
C7: 400uF; E2,5-6
ENC_R: PINHD-1X3; 1X03
EN_L: PINHD-1X3; 1X03
ESP_L: PINHD-2X9; 2X09
ESP_R: PINHD-2X9; 2X09
GD|RX|TX: PINHD-1X3; 1X03
IC1: LM317TS; 317TS
IN: PINHD-1X7; 1X07
LED1, LED2: TLLG4400; LED3MM
M_OUT: PINHD-1X4; 1X04
OUT: PINHD-1X7; 1X07
PWR_SWC: TL32PO; TL3XPO
R1: 12k; 0207/10
R2: 390; 0207/10
R3: 240; 0207/10
R4, R5: 0.6k; 0207/10
U3: USB""; USB-MICRO-SMD

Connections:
EN1: ESP_L.8, IN.3
EN2: ESP_L.10, IN.5
ENC_L: EN_L.3, ESP_L.4
ENC_R: ENC_R.3, ESP_L.6
GND: C4.2, C5.-, C6.-, C7.-, ENC_R.1, EN_L.1, ESP_R.1, IN.1, LED1.K (C), LED2.K (C), OUT.1, R2.1, U3.GND1 (GND)
LED1: ESP_R.7, R5.1
LED2: ESP_R.9, R4.1
unnamed: M_OUT.1, OUT.3
unnamed: M_OUT.2, OUT.4
unnamed: M_OUT.3, OUT.5
unnamed: M_OUT.4, OUT.6
unnamed: ESP_R.4, GD|RX|TX.1
unnamed: ESP_R.6, GD|RX|TX.2
unnamed: IC1.1 (ADJ), R2.2, R3.2
unnamed: ESP_R.8, GD|RX|TX.3
unnamed: LED2.A, R4.2
unnamed: PWR_SWC.2, U3.VBUS1 (VBUS)
unnamed: ESP_R.3, R1.1
unnamed: LED1.A, R5.2
PH1: ESP_L.5, IN.4
PH2: ESP_L.11, IN.6
VCC: C4.1, C7.+, ENC_R.2, EN_L.2, ESP_R.2, IC1.2 (OUT), IN.2, R1.2, R3.1
VDD: C5.+, C6.+, IC1.3 (IN), OUT.2, PWR_SWC.1 (O)

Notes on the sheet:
GND VCC EN2 PH2 EN1 PH1 MD
GND VIN O2 O1 O2 O1 VM
M1 M1 M2 M2
RX TX GND
GND VCC OUT
3.3 TXD RXD GND
IO4 IO2
GND EN
IO23 IO22
IO19 IO5
IO16 IO0
IO5
IO4
SVN IO35
IO33 IO26
IO14 IO13
SD3 CLK
SD1
SVP IO34
IO32 IO25
IO27 IO12
SD2 CMD
SD0

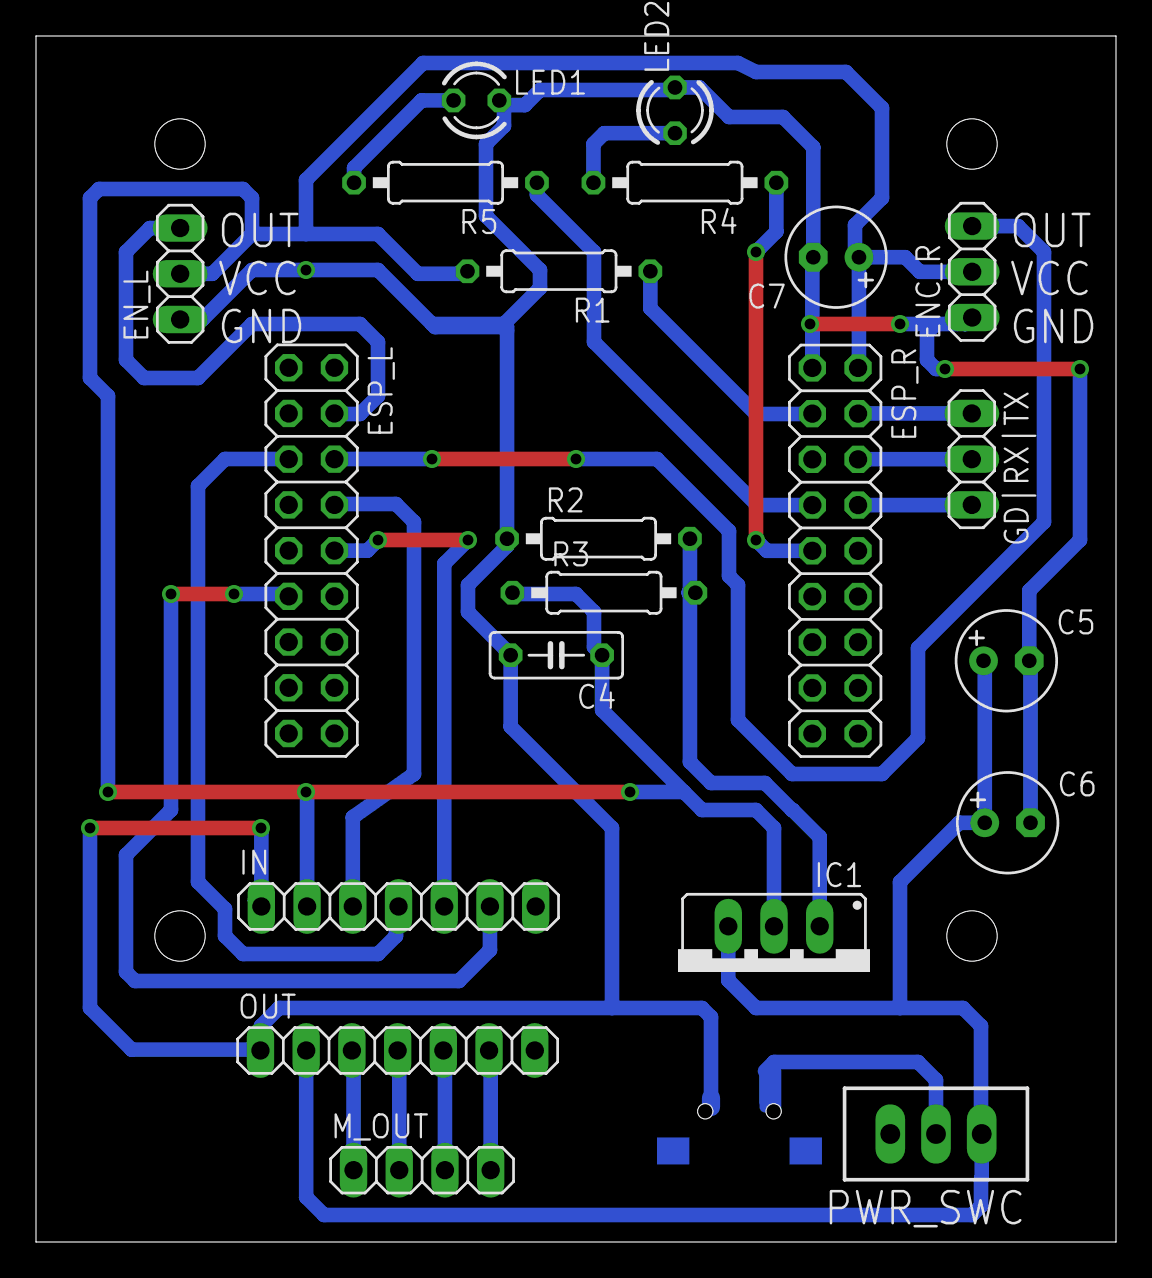
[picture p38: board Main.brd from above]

Board: 2 copper layers, 60.0 x 67.0 mm, 22 parts (1 on the bottom side), 23 nets.

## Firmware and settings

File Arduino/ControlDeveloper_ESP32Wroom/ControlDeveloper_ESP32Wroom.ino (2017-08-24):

#include <Arduino.h>
#include <esp32-hal-dac.h>
#include <WiFi.h>

//Enable this to get info via serial port
#define DEBUG true

#include "connection.h"
#include "DRV8835_Driver.h"
#include "QRE1113_Driver.h"
#include "my_util.h"
#include "PID.h"

//Functions prototypes
void parseData();

//Commands structure and create a variable
struct Command
{
	String name;
	int degrees;
	long duration;
	int speed;
	int nrSteps;
	int nrRepetition;

	//private data regarding command execution
	//Make this false when command was executed and make true when command was received
	bool updated = false;
}command;

void setup()
{
	if(DEBUG)
	{
		Serial.begin(115200);
		Serial.println("---STARTING---");
	}

	//initialize motors
	motors.attachM1Pin(25, 33, true);	// en, ph	-> left motor
	motors.attachM2Pin(27, 13, true);	// en, ph	-> right motor
	motors.init();
	motors.brake();
	
	//initialize connection
	conn::setupAP();
	server.begin();
	conn::waitForServerClients();
	//*/
}

void loop()
{
	//Updating encoders values
	leftEncoder.update();
	rightEncoder.update();
	
	
	//Wifi link - check if client is still connected
	if (!client || !client.connected())
		conn::waitForServerClients();

	//Check if client have a command for us
	if (client.available())
	{
		String recvMsg = conn::readString();
		Serial.print(recvMsg.substring(0, recvMsg.length() - 1));	//Removing \n from the end

		//Send feedback to Java App telling that we received command.
		conn::writeString("Command(s) received...");

		//Try to parse received data                                                                                                                                                                                                                                                                                            
		parseData(recvMsg) ? Serial.println("Data parsed!") : Serial.println("Failed to parse data!");
		
		//Try to execute command
		if (execute_command())
			conn::writeString("Command(s) executed...");
		else
			conn::writeString("Command(s) failed (NOT)...");
	}
	//*/
	//Allow commands execution from serial
	if (DEBUG && Serial.available() > 0)
	{
		String data = Serial.readString();
		if (!parseData(data))
			Serial.println("Failed to parse!");

		leftEncoder.currSteps = 0;
		rightEncoder.currSteps = 0;

		if (!execute_command())
			Serial.println("Failed to execute!");
	}

	//Precious debug info
	if (DEBUG) printEncoderSpeed(500);	//print data every 0.5 seconds
}

bool parseData(String data)
{
	//Format of data we receive: >>[G;-100;0] or [D;-100;0]#[R;-100;0]#[P;-100;0]
	if (data.length() < 7)
	{
		command.updated = false;
		return false;
	}

	//Geting string between barrecks: [*]
	data = data.substring(data.indexOf('[') + 1);
	data = data.substring(0, data.indexOf(']'));

	command.name = getStringPartByNr(data, ';', 0);
	command.name.toUpperCase();

	if (command.name == "D")
	{
		command.degrees = getStringPartByNr(data, ';', 1).toInt();
	}
	else if (command.name == "G")
	{
		command.speed = getStringPartByNr(data, ';', 1).toInt();
		command.duration = getStringPartByNr(data, ';', 2).toInt();
	}
	else if (command.name == "R")
	{
		command.nrSteps = getStringPartByNr(data, ';', 1).toInt();
		command.nrRepetition = getStringPartByNr(data, ';', 2).toInt();
	}
	else if (command.name == "P")
	{
		command.duration = getStringPartByNr(data, ';', 1).toInt();
	}
	else
	{
		command.updated = false;
		return false;
	}

	command.updated = true;
	return true;
}

bool execute_command()
{
	//reset encoders
	leftEncoder.currSteps = 0;
	rightEncoder.currSteps = 0;

	if (command.updated == false)
		return false;

	if (command.name == "D")
	{
		command_direction();
		return true;
	}
	else if (command.name == "G")
	{
		command_gear();
		return true;
	}
	else if (command.name == "R")
	{
		command_repetition();
		return true;
	}
	else if (command.name == "P")
	{
		command_pause();
		return true;
	}
	else
	{
		command.updated = false;
		return false;
	}
}

void command_direction()
{
	Serial.println("Executing direction...");
	Serial.println("Degree: " + String(command.degrees));

	//Firstly we have to map speed. This will prepare variables and all thr stuff for motors
	mapSpeed(10);	//the speed used to execute this command

	//degrees to steps conversion
	//26 = 180 degrees
	int steps = 26;	//90

	//Degees can be [-90,90], where -90 = 90degrees to left and 90 = 90degrees to right
	if (command.degrees < 0)
	{
		steps = map(command.degrees, 0, -90, 0, 13);
		computeSteps(steps, DRV8835::BACKWARD, 1, DRV8835::FORWARD);
	}
	else if (command.degrees > 0)
	{
		steps = map(command.degrees, 0, 90, 0, 13);
		computeSteps(steps, DRV8835::FORWARD, 1, DRV8835::BACKWARD);
	}

	mapSpeed(0);		//set speed to 0
	motors.brake();		//brake motors

	//Also reset encoders
	leftEncoder.currSteps = 0;
	rightEncoder.currSteps = 0;

	command.updated = false;
	Serial.println("SUCCESS\n");
}

void command_gear()
{
	Serial.println("Executing gear...");
	Serial.println("Speed: " + String(command.speed) + " Duration: " + String(command.duration));

	//Firstly we have to map speed. This will prepare variables and all thr stuff for motors
	mapSpeed(command.speed);

	//We need to go in a direction for a specific amount of time
	int startTime = millis();	//store time execution starts.
	do
	{
		//Need to update encoders
		leftEncoder.update();
		rightEncoder.update();

		motors.setM1Speed(speed);
		updateSlaveMotor(0);					//slave motor will pick up speed automatically from encoders measuements in order to get a smooth movement
		
		printEncoderSpeed(500);	//print data every 0.5 seconds -> good for debugging
	} while(millis() - startTime < command.duration);

	
	//stop motor which finished his steps - and update encoders to make sure we keep counting
	int leftSteps = leftEncoder.currSteps;
	int rightSteps = rightEncoder.currSteps;
	int error = (leftSteps > rightSteps) ? leftSteps - rightSteps : ( (rightSteps > leftSteps) ? rightSteps - leftSteps : 0);
	bool m1BrakeEn = false, m2BrakeEn = false;	//remember which motor is stopped

	if (error != 0)
	{
		if (leftSteps < rightSteps)	//if left motor needs to make more steps
		{
			//motor 1 needs to make some more steps and motor2 needs brake
			while (leftSteps < rightSteps)
			{
				leftEncoder.update();
				leftSteps = leftEncoder.getSteps();
				motors.setM1Speed(speed);

				//and stop the other motor
				motors.setM2Speed(0);
			}
		}
		else	// otherwise rightSteps < leftSteps
		{
			while (rightSteps < leftSteps)
			{
				rightEncoder.update();
				rightSteps = rightEncoder.getSteps();
				motors.setM2Speed(speed);

				//stop the other motor
				motors.setM1Speed(0);
			}
		}
	}

	//brake motors - no more steps after gear was executed - if capacitors are not exactly the same
	// as required in shematics, disable this. it will reset board due to high amount of required current to brake;
//	if( !m1BrakeEn) motors.setM1Speed(speed*-1);
//	if( !m2BrakeEn) motors.setM2Speed(speed*-1);
//	delay(10);

	mapSpeed(0);		//set speed to 0
	motors.brake();		//brake motors
	
	command.updated = false;
	Serial.println("SUCCESS\n");
}

void command_repetition()
{
	Serial.println("Executing repetition...");
	Serial.println("nrSteps: : " + String(command.nrSteps) + " nrRepetitions: " + String(command.nrRepetition));

	//Repetition? Not sure...

	command.updated = false;
	Serial.println("SUCCESS\n");

}

void command_pause()
{
	Serial.println("Executing pause...");
	Serial.println("Duration: " + String(command.duration));
	
	//Pause means to delay program
	delay(command.duration);

	//Set this marker to show when new commands were received
	command.updated = false;

	Serial.println("SUCCESS\n");
}

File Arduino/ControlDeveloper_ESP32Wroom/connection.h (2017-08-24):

#ifndef connection_h
#define connection_h

#include <Arduino.h>
#include <WiFi.h>
#include <WiFiServer.h>
#include <WiFiClient.h>

//AP Credentials. Those will be used in our Java applicaion.
const char *AP_Name   = "LAB_ROVER_3";
const char *AP_Passwd = "LabRover@Passwd";

//Led which will indicate data transfers
int connectionLedIndicatorPin = 19;
int trafficLedIndicatorPin = 22;

//Setting up server on specified port
WiFiServer server(1337, 1);
WiFiClient client;

//Connection manage namespace prototype
namespace conn
{
	void setupAP();
	void waitForWifiClients();
	void waitForServerClients();
	bool writeString(String data);
	String readString();
	bool isWritable();
	void connectionLedIndicator();
	void writePeriodicData(String data, int interval = 1000);
}

namespace conn
{
	//function used to initialize WiFi module in AP Mode
	void setupAP()
	{
		//Leds PINS are set as OUTPUT
	    pinMode(trafficLedIndicatorPin, OUTPUT);
	    pinMode(connectionLedIndicatorPin, OUTPUT);

		//Configure chip on AP mode
		Serial.print("Configuring AP...");
		WiFi.mode(WIFI_AP);
		bool AP_Created = WiFi.softAP(AP_Name, AP_Passwd);
		AP_Created ? Serial.println( "done" ) : Serial.println( "failed" );

		//Print AP IP Address
		IPAddress apIP = WiFi.softAPIP();
		Serial.print("AP IP Address: "); Serial.println(apIP);
	}

	//Loop to wait for wifi clients in case of connection lost
	void waitForWifiClients()
	{
		Serial.print("Waiting for Wi-Fi clients...");
		while(WiFi.softAPgetStationNum() == 0)
		{
			delay(600);
			connectionLedIndicator();
		}
		Serial.println("done");

		pinMode(trafficLedIndicatorPin, OUTPUT);
		digitalWrite(trafficLedIndicatorPin, LOW);
		digitalWrite(connectionLedIndicatorPin, LOW);
	}

	//Loop to wait for clients to open tcp sockets
	void waitForServerClients()
	{
		//Maybe socket stopped because link was lost because of WiFi disconnect
		delay(100); //We need this delay to get update values of WiFi Clients
		if(WiFi.softAPgetStationNum() == 0)
			conn::waitForWifiClients();

		Serial.print("Waiting for socket clients...");
		while(!client || !client.connected())
		{
			connectionLedIndicator();
			delay(250);
			client = server.available();

			//In the meanwhile AP may be disconnected - we may want to check
			if(WiFi.softAPgetStationNum() == 0)
			{
				Serial.println("failed");
				conn::waitForWifiClients();
				Serial.print("Waiting for socket clients...");
			}
		}
		client.setNoDelay(true);
		Serial.println( "done" );

		pinMode(trafficLedIndicatorPin, OUTPUT);
		digitalWrite(trafficLedIndicatorPin, LOW );
		digitalWrite(connectionLedIndicatorPin, LOW);
	}

	//Function to write to client TCP socket
	bool writeString(String content)
	{
		digitalWrite(trafficLedIndicatorPin, HIGH);

		if(!isWritable())
		{
			digitalWrite(trafficLedIndicatorPin, LOW);
			return false;
		}

		int result = client.println(content); delay(2);
		if(result < 1)
		{
			digitalWrite(trafficLedIndicatorPin, LOW);
			return false;
		}

		digitalWrite(trafficLedIndicatorPin, LOW);//*/
		return true;
	}

	//Read string from client TCP socket
	String readString()
	{
		digitalWrite(trafficLedIndicatorPin, HIGH);
		String result = client.readString();
		digitalWrite(trafficLedIndicatorPin, LOW);//*/
		return result;
	}

	//check if client socket is writable
	bool isWritable()
	{
		int result = client.print(">");
		delay(4); //wait for register with error to be filled up
		if(!result)
			return false;

		result = client.print('>');
		delay(4); //wait for register with error to be filled up
		if(!result)
			return false;

		return true;
	}

	//Indicate via leds connection status
	void connectionLedIndicator()
	{
		static bool lastTime = false;	//remember last state of button
		static long previousMillis = 0;
		if (millis() - previousMillis > 400)
		{
			previousMillis = millis();

			//pinMode(connectionLedIndicatorPin, INPUT);
			//bool currStatus = digitalRead(connectionLedIndicatorPin);
			//pinMode(connectionLedIndicatorPin, OUTPUT);
			digitalWrite(connectionLedIndicatorPin, !lastTime);
			lastTime = !lastTime;
		}
	}

	//Write periodic some data
	void writePeriodicData(String data, int interval)
	{
		static long previousMillis = millis();
		if (millis() - previousMillis > interval)
		{
			previousMillis = millis();
			conn::writeString(data);
		}
	}
}
#endif

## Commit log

2017-06-20 Eagle design changed.
    [Wheel - (c) Anian B.stl]
2017-06-27 Added code for ESP32Wroon
2017-06-27 Added encoders on Eagle Project
    [Main.brd, Main.sch]
2017-06-28 Eagle proj - redesigned
    [Main.brd, Main.sch]
2017-06-28 3D Design is just perfect now ^_^
    [RoverFrame.stl]
2017-06-28 Finished eagle board!
    [Main.brd, Main.sch]
2017-06-28 Added PCB Pinmap and Readme
    [Main.brd]
2017-06-29 Added schematic picture
2017-06-29 Board picture
2017-06-29 Final version of Eagle board
    [Main.brd, Main.sch]
2017-06-29 Updated 3D Design
    Larger holes to fix motors.
    [RoverFrame.stl]
2017-06-29 IR Sensors calibrated with wheels
2017-07-02 PID
    Pid works pretty good at power 80.
2017-07-02 Motors Driver Lib - Changed
2017-07-03 More stable version of PID
    Works perfect in interval [45-75]
2017-07-05 Bugs in Eagle Design were corrected!
    [Main.brd]
2017-07-05 Working version of PID with computeSteps(nr) function.
    Known bug: Compute steps function workd only forward. On different
    directions there is a conflicat between updateSlaveMotor() and
    computeSteps(...)
    [PID_Rover.ino]
2017-07-05 All functions works perfectly!
    Patched bug in computeSteps(...) now function works like a charm and
    uses pid function to make rotation more linear.
    [PID_Rover.ino]
2017-07-06 **** **First RELEASE** ****
    Fully working version of code and Eagle design!
    [Main.brd, Main.sch]
2017-07-06 ****Release*** NO MORE Radio bugs
    [Main.brd, Main.sch]
2017-07-07 No more bugs on schematic
    The left motors starts no more before init() sequence.
2017-07-07 Arduino password and ap name added on readme
2017-07-11 Added switch to components list
2017-07-11 Eagle PCB Redesigned
    * Routes were optimized
    * Space for heat sink added
    * Added Power ON/OFF switch
    [Main.brd, Main.sch]
2017-07-20 Added screws on components list
